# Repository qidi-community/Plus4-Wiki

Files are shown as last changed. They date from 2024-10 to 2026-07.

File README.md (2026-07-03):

# Qidi Community Plus4 Wiki

This is a summary collection of various config tweaks, print profiles, the discussion of, and
links to various printable models that have been developed for improving the user experience
of the Qidi Plus4 3D printer.

## Official Qidi Wiki

### [Qidi Plus 4 Wiki/Support Page](https://wiki.qidi3d.com/en/X-Plus4)

---

## Issues and Possible Fixes

### [Plus4 System Performance Tuning](./content/system-tuning/README.md) or [Alternative version](./content/system-tuning-alt/README.md)

### [Adaptive Main Board Cooling configuration](./content/adaptive-main-board-cooling)

### [SSH Security](./content/ssh-security/README.md)

### [Adding Beacon3D](./content/bed-scanning-probes/Beacon3D/RevH-Normal)

> [!TIP]
> Qidi's 1.7.0 and later updates introduced breaking changes that crash klipper if you have cartographer probe installed. Read the updated cartographer guide below to learn more.
### [Adding Cartographer](./content/bed-scanning-probes/cartographer3d)

### [Modular Tool-Head Mod](./content/modular-toolhead/README.md)

### [Making Z-Offset Permanent](./content/making-z-offset-permanent)

### [Conditional purging and pei wiping to address the cracking of nozzles with ceramic heat-breaks](./content/conditional_purging_and_wiping/README.md)

### [Warming the Chamber Faster!](./content/tuning-for-40-percent-heater-power/README.md)

### [More Accurate Chamber Temperature Measurements](./content/chamber-heater-investigation/README.md)

### [Broken touchscreen firmware](./content/display-firmware-repair/README.md)

---

## (Mostly) Defunct fixes that have been fixed with newer shipping Plus4 models

### [PLA/PETG Heat-creep clogging](./content/nozzle-clogging-tips/README.md) - Fixed by using nozzles with ceramic heatbreaks

### [Chamber Heater Issue](./content/chamber-heater-issue/README.md) - Largely addressed by the v1.6.0 and later firmware

### [SSR Upgrade Mod](./content/heater-ssr-upgrade/README.md) - All Plus4's manufactured after Dec 2024 should already have the fixed SSR's

---

## Printer Configuration Tweaks

### [SSH Access](./content/ssh-access/README.md)

### [Adaptive Chamber Heater Fan](./content/adaptive-chamber-heater-fan/README.md)

### [Dynamic Chamber Temperature Manager](./content/chamber-temperature-manager/README.md)

### [Enhanced Stepper Motor Configuration](./content/stepper-motor-tweaks/README.md)

### [Tweak to Square Corner Velocity](./content/square-corner-velocity/README.md)

### [Enabling KAMP Purge Line](./content/kamp-purging)

### [Enabling SCREWS_TILT_CALCULATE](./content/Screws-Tilt-Adjust/)

### [Better Bed Meshing](./content/more-accurate-bed-meshing/README.md)

### [Disable Wifi Adapter](./content/8188gu-blacklist/README.md)

### [Temperature Change Chimes](./content/temp-chime/README.md)

### [Secure Remote Access](./content/secure-remote-access/README.md)

### [Notes on Heat Soak](./content/Auto Heat Soak for Stock Sensors/README.md)

### [Warp free ASA / ABS prints](./content/warp-free-asa-abs-prints/README.md)

## Orca Slicer Configuration

### [Orca Slicer Settings](./content/orca-slicer-settings)

## Qidi Box

### [Bunny Box - open source Qidi Box using Happy Hare](https://github.com/Wazzup77/Bunny-Box)

---

## Printable Models

### [Ejecta Chute and Catch Bucket](https://www.thingiverse.com/thing:6789666)

### [Ejecta Chute and Catch Bucket - No heatset inserts remix](https://www.thingiverse.com/thing:6794632)

### [Fan duct for the hotend heatsink](https://www.thingiverse.com/thing:6782612)

### [Mainboard cooling](./content/mainboard-cooling/README.md)

### [Mainboard Rear cover that allows use of an 80mm fan](https://www.thingiverse.com/thing:6787302)

### [Lid Hangers](https://www.printables.com/model/1025183-qidi-plus-4-lid-hanger)

### [Filter Exhaust Blocker](https://www.printables.com/model/1037302-qidi-plus-4-filter-exhaust-blocker)

### [Rear Chamber Seal](https://www.printables.com/model/1040774-qidi-plus-4-rear-chamber-cover)

### [HEPA/Activated Carbon filtration system](https://www.printables.com/model/1022271-qidi-plus-4-filtration-system)

### [Exhaust adapter attachment (with CAD)](https://www.printables.com/model/1040218-qidi-plus-4-exhaust-adapter)

### [Lid prop](https://www.printables.com/model/1039528-qidi-plus4-lid-prop)

### [4 inch Duct extraction adapter](https://www.printables.com/model/1036212-qidi-plus-4-4-inch-duct)

### [Hole blocking plate](https://www.printables.com/model/1039152-qidi-4-plus-ports-cover)

### [Push In Place Door Sealing Strip](https://www.thingiverse.com/thing:6801577)

### [Belt Tensioners](https://www.printables.com/model/1044712-qidi-plus4-belt-tensioners/files)

### [WIP - A better chamber thermal sensor mounting position](https://www.thingiverse.com/thing:6802256)

### [Articulating No Hands Door Seal (paid)](https://cults3d.com/en/3d-model/tool/plus4-articulating-no-hands-door-hinge-seal)

### [Articulating No Hands Door Seal (free)](https://www.printables.com/model/1271100)

### [Filament Tangle Sensor Disabler Clip](https://www.printables.com/model/1767439-qidi-plus-4-filament-tangle-blocker-clip)

---

## Additional Software

### [Klippain Shake & Tune v5.1.1 - Qidi Plus 4 Compatible Version](https://github.com/qidi-community/klippain_v511_for_qidi_plus4)

### [(Retired) Klippain Shake & Tune v4.1.0 - Qidi Plus 4 Compatible Version](https://github.com/qidi-community/ShakeTune-For-Plus4)

---

## Aftermarket Parts

### [Replacement hotend heatsink fan - GDSTime GDA30105F (US Store)](https://west3d.com/products/gdstime-dc-24v-30x30x10-axial-fan-24v-gda30105f-dual-ball-bearing-1200rpm-1w-06a-xh2-54)

### [Replacement hotend heatsink fan - GDSTime GDA30105F (EU Store)](https://www.hotend.eu/p/gdstime-axial-fan-sleeve-3010-24v)

### [Replacement hotend heatsink fan - GDSTime GDA30105F (CN Store)](https://www.aliexpress.com/item/1005002857100082.html)

### [Replacement 80 mm mainboard fan - ANVISION (Amazon US)](https://www.amazon.com/ANVISION-2-Pack-Brushless-Cooling-Bearing/dp/B0C18G953Z)

---

## Maintenance Tips

### [Adjusting Belt Tension](./content/adjusting-belt-tension)

### [Lubing Idler Bearings](https://drive.google.com/file/d/1_KHpMQJNxle0u21L5dIt-LYLbkvVnGiD/view)

### [Lubing Rods and Screws](./content/lube-rods-screws)

---

## Hardware Fixes

Some of the first release batches of the Plus 4 have had the occasional hardware issue.
Qidi assures that all customers who contact Qidi support will be looked after.
In the meantime, here are a number of known fixes for the issues that some early adopters are experiencing.

### [Official Qidi Toolhead Bearing Fix](https://drive.google.com/drive/folders/1O0PR0vbxy0Tv7vgcNma1JERQyz9Ir3xW)

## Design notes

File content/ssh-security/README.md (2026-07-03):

# Securing SSH Access

> [!CAUTION]
> FOLLOWING THESE INSTRUCTIONS HAVE THE POTENTIAL TO PERMANENTLY LOCK YOU OUT OF `ssh` ACCESS. PLEASE FOLLOW ALL INSTRUCTIONS CAREFULLY, NOTE DOWN ALL PASSWORDS, AND BACKUP ANY PRIVATE/PUBLIC KEYS AS APPLICABLE.
>
> If you become locked out due to losing access to your password or public/private key-pairs, the only way to restore access would be to perform a factory result with fresh firmware from QIDI and there is no known way to regain access. Only proceed if you can understand and can bear or mitigate the potential risks involved.

By default, the QIDI Plus4 ships with an insecure SSH configuration, allowing simple password access to both the `root` and `mks` accounts. More details on gaining SSH access can be found [here](../ssh-access/README.md).

As such, any bad actor on your local network or with access to the printer's SSH port is able to gain trivial access with full control, allowing for remote code execution, installation of malware, modifying Klipper configs, etc. As such, it's important to secure SSH access to the printer through:

- Changing default passwords [High Importance]
- Disabling root login [High Importance]
- Setting up public/private key authentication [Moderate Importance]
- Disabling password-based SSH login [Moderate Importance]
- Ensuring local-only SSH access through router/network/firewall configuration [Low Importance - Out of Scope]

It is recommended to perform the first four steps in conjunction, as they involve minimal edits to a single file and vastly improve security of your machine.

## Change Default Passwords

The default password for both `root` and `mks` accounts on the Plus4 is `makerbase`. This should be changed for the `mks` password as soon as practicable if the printer is on the network. 

### Prerequisites
- The IP Address of the printer (obtained through the Printer network screen or your router)
- Ability to SSH (WSL on Windows, Terminal on MacOS / Linux)

### Process

SSH into your printer's `mks` account:

```
ssh mks@<ip-address>
```

Type `passwd` to change the password of the `mks` account. It's recommended to use a complex password here, as the `mks` account can gain privileged access through this password.

If you want to keep `root` login, then it is recommended to change the `root` account password too. You can gain `root` account access from the `mks` account with the below command:

```
sudo -i
```

You will be prompted to type the new password that you just set. Then, run `passwd` as the `root` user to change the `root` password. Ideally, it should be different from the `mks` password to prevent simultaneous compromise, though such risks are low. 

## Disabling Root Login

It is recommended to disable the ability to log into the printer as the `root` user, which has superuser privileges. Instead, all SSH logins should be done through a normal user account, and then escalated to `root` with `sudo` as needed. This helps to reduce one potential vector of compromise. 

### Prerequisites
- The IP Address of the printer (obtained through the Printer network screen or your router)
- Ability to SSH (WSL on Windows, Terminal on MacOS / Linux)
- Use of `nano`, `vim,` or `vi` text editor in the command line

### Process

SSH into your printer's `mks` account.

Edit the file found at `/etc/ssh/sshd_config` with `sudo` privileges:

```
sudo nano /etc/ssh/sshd_config
```

Find the line beginning with `PermitRootLogin` and change "yes" to "no". Your end result should look like the below. Mine was found on line 32.

```
PermitRootLogin no
```

Save and exit. Restart the `ssh` daemon with:

```
sudo systemctl restart ssh
```

## Set up Private / Public Key Authentication

Traditionally, SSH authentication is handled with user account passwords. However, passwords can be easily stolen, guessed, or phished and are therefore a less secure means of authentication. Instead, SSH has support for public/private key authentication, whereby a machine generates a key-pair, and the public key of such keypair is shared with the server, and the private key is kept hidden locally. Since these public/private keys are kept cryptographically secure and the private key does not leave your machine in any situation, this is a more resilient form of authentication.

Further details on public/private key authentication is out of scope and can be found [here](https://en.wikipedia.org/wiki/Public-key_cryptography)

As such, it's recommended to enable public/private key authentication to SSH into the printer as opposed to the password-based authentication. You also no longer need to type in your password when SSHing in.

### Prerequisites
- An SSH key-pair has been generated on your computer
  - The exact process varies between OS. Some basic guides are linked below.
    - [WSL/Windows](https://www.howtogeek.com/762863/how-to-generate-ssh-keys-in-windows-10-and-windows-11/)
    - [MacOS/Linux](https://devopscube.com/generate-ssh-key-pair/)
- The IP Address of the printer (obtained through the Printer network screen or your router)
- Ability to SSH (WSL on Windows, Terminal on MacOS / Linux)
- (Optional) The `ssh-copy-id` command **or** a command line text editor (nano / vi / vim)

### Process

There are two options to install the SSH key: (i) automatically with the `ssh-copy-id` command or (ii) manually. If you have the `ssh-copy-id` command in your local computer's command line, it is recommended to use that as it greatly simplifies the process. You can also copy the key manually if preferred, but offers no functional benefits. Most machines will have the `ssh-copy-id` command.

#### Automatic Installation

Once you have generated your SSH key-pair or if you are using an existing SSH key-pair, you will need to copy the ***public*** key of the key-pair onto your printer. ***DO NOT*** under any circumstance, allow your ***private*** key to leave your machine. That is equivalent of a password and should be treated as such. 

Copy the public key to the printer with the following command:

```
ssh-copy-id mks@<ip-address>
```

You will be prompted from the password for the `mks` account. This will install the public key automatically into the `mks` account. You should now be able to `ssh` into the `mks` account without needing to input a password.

#### Manual Installation

If your machine does not have the `ssh-copy-id` command, you will need to copy the key manually. First of all, find the ***public*** key that you generated. Copy the entirety of the public key file. You will need to paste that in a later step.

SSH into your printer:

```
ssh mks@<ip-address>
```

Edit the file found at `~/.ssh/authorized_keys`. This is the listing of all SSH public keys which are allowed to access the printer. You do not need superuser privilege to edit this file.

```
nano ~/.ssh/authorized_keys
```

Paste in the ***public*** key that you copied earlier. You have now installed the SSH public key and you should be able to `ssh` into the `mks` account without needing to input a password.

## Disable Password Authentication

If you are using private / public key authentication with your printer and do not need password authentication, it is recommended that you disable the ability to SSH into the printer with a password. This vastly improves security, particularly if your password is less complex, reused, or easy to guess. While a strong password mitigates the risk significantly, it is still recommended to remove SSH password access to reduce the attack surface. 

### Prerequisites
- The IP Address of the printer (obtained through the Printer network screen or your router)
- Ability to SSH (WSL on Windows, Terminal on MacOS / Linux)
- SSH private / public key authentication set up and working
- Use of `nano`, `vim,` or `vi` text editor in the command line

#### Warning!!!

If you disable password authentication, you will not be able to SSH into your printer except with the private / public key(s) you have set up. Please be mindful that if you lose your private / public key access, you will not be able to SSH into the printer at all, and will need to undergo a complete factory reset. QIDI will not be able to recover access for you, and there is no (known) way to bypass this. Before doing this, it is recommended you have at least two devices with different SSH key-pairs set up for access, in case you lose your primary device.

### Process

SSH into your printer:

```
ssh mks@<ip-address>
```

Edit the file found at `/etc/ssh/sshd_config` with `sudo` privileges:

```
sudo nano /etc/ssh/sshd_config
```

Make the following changes to these SSH parameters within the file:

```
PasswordAuthentication no
ChallengeResponseAuthentication no
UsePAM no
```

`ChallengeResponseAuthentication` may already be set to `no`. If so, no changes to that line are needed.

Save and exit. Restart the `ssh` daemon with:

```
sudo systemctl restart ssh
```

Password login should now be disabled for the printer, and you must login with one of the existing private / public key pairs.

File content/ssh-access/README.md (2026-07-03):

# How to access your Plus 4 through SSH

SSH access is needed to interact with the Klipper configuration system. You will specifically need to SSH into your printer to add Klipper extensions.

To log into your printer, first detrmine it's IP address from the front panel's network tab.

Then open a shell (or Terminal on Windows) and type:

```ssh mks@x.x.x.x``` 

Where x.x.x.x is the IP address.

The password is **makerbase**

Common config files are in /home/mks/printer_data/config

You can also use popular FTP client filezilla, with Host sftp://IP_ADDRESS (user and pass as above) , then right click a file, choose View/Edit, when you save, go back to filezilla and it will ask if you want to re-upload changes.

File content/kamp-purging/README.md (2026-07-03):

# Enabling KAMP Purging

KAMP Purging draws a single short ~30mm long, ~2mm wide, and ~0.8mm tall line near the front left of the area that the model will occupy.

This serves a similar purpose to the stock Qidi purge patterns by clearing the nozzle of any oozing material just before starting the first print object.

The KAMP Purge line uses about the same amount of filament as the stock Qidi purge pattern.

The main complaint about the stock Qidi purge pattern is that it can be difficult to remove cleanly. This can result in touching the build surface area excessinvely, possibly leaving oily residue from fingers. In turn, _this_ can then affect surface adhesion quality for future prints until the plate is cleaned/washed again.

The KAMP purge line, being thicker and shorter, makes it easy to flick off the build surface with a fingernail, resulting in less contact with the build plate.

** While these are valid advantages, you can also try using a 5-10 loop skirt, as this lets you check/test your 1st layer z-height across the whole build area perimeter and is easier to remove than the default single line. - hayden.

## How to Enable

TL;DR Doing the following will enable the `LINE_PURGE` macro in Klipper, which we will use later.

First we must edit the `KAMP_Setting.cfg` file, which lives in the same directory as `printer.cfg`

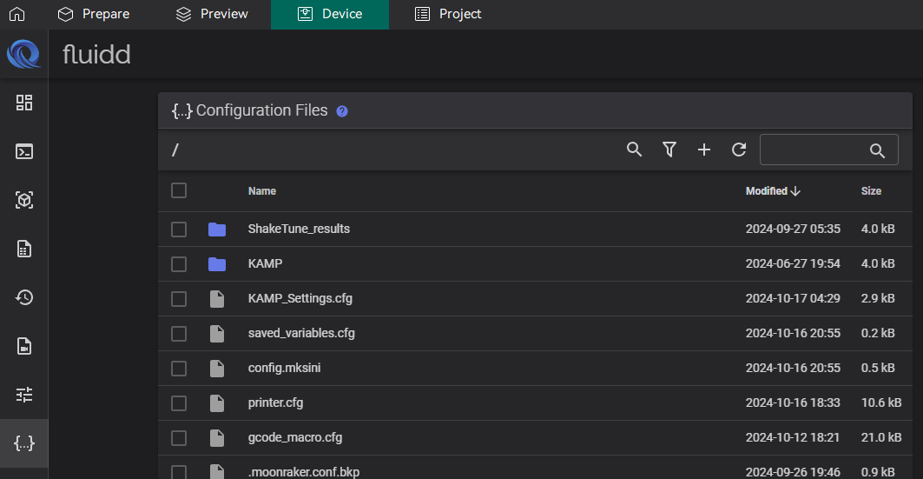
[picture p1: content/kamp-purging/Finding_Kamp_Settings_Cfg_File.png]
Where to find KAMP_Settings file


or go to directory `/home/mks/printer_data/config` if you're using [SSH](https://github.com/qidi-community/Plus4-Wiki/tree/main/content/ssh-access).

Uncomment the line `[include ./KAMP/Line_Purge.cfg]`.

> [!TIP]
> If you plan on printing with TPU, I also recommend changing the `variable_flow_rate` setting to a value of `4`.
The default of `12` here is way too high for TPU, and possibly some other filament types, and can cause oozing and extruder issues.

### Restart the Printer

If you've edited the files through Fluidd, Use the orange "Save & Restart" button up top

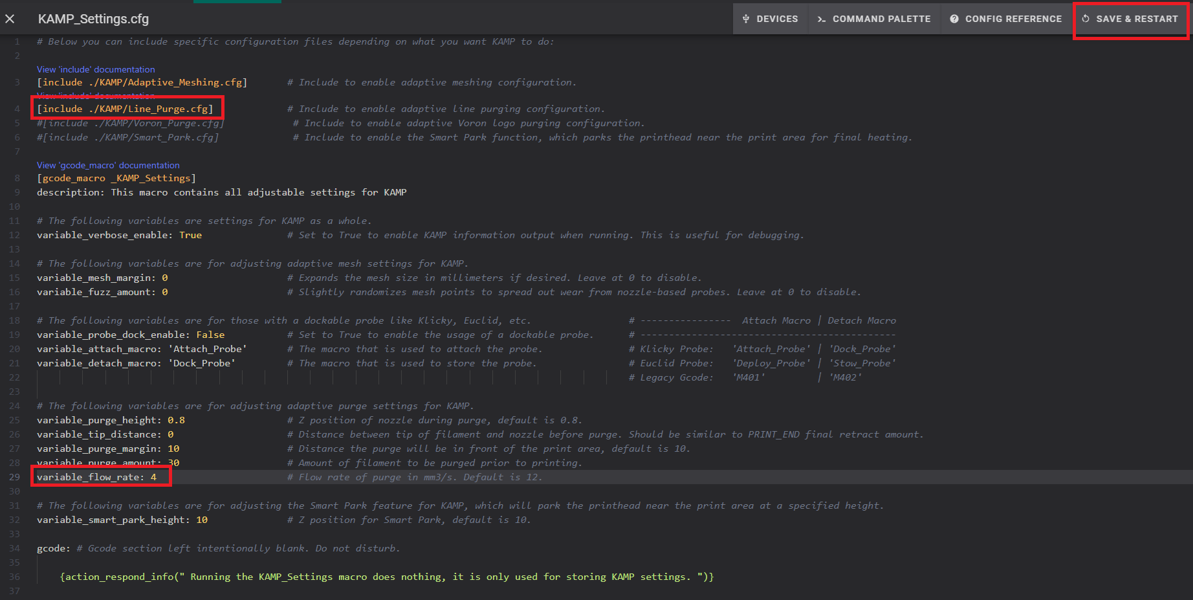
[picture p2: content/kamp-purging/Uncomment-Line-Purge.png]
Uncommenting KAMP's Line Purge Config


If you used SSH, please note that the files you've just edited are not necessarily written to disk yet. 
To force this to happen, run the command `sync`. If that comes back with no further remarks and has an exitcode of `0`, you can powercycle the printer.

SSH check exitcode sync

## Editing the Printer's Start G-Code in the slicer

The stock Qidi purge pattern is created by a set of lines in the Printer's Start G-Code definition in the slicer.

The Qidi Purge Pattern G-Code will look like this:

```
G0 Z[initial_layer_print_height] F600
G1 E3 F1800
G1 X{(min(print_bed_max[0] - 12, first_layer_print_min[0] + 80))} E{85 * 0.5 * initial_layer_print_height * nozzle_diameter[0]} F3000
G1 Y{max((min(print_bed_max[1] - 3, first_layer_print_min[1] + 80) - 85), 0) + 2} E{2 * 0.5 * initial_layer_print_height * nozzle_diameter[0]} F3000
G1 X{max((min(print_bed_max[0] - 12, first_layer_print_min[0] + 80) - 85), 0)} E{85 * 0.5 * initial_layer_print_height * nozzle_diameter[0]} F3000
G1 Y{max((min(print_bed_max[1] - 3, first_layer_print_min[1] + 80) - 85), 0) + 85} E{83 * 0.5 * initial_layer_print_height * nozzle_diameter[0]} F3000
G1 X{max((min(print_bed_max[0] - 12, first_layer_print_min[0] + 80) - 85), 0) + 2} E{2 * 0.5 * initial_layer_print_height * nozzle_diameter[0]} F3000
G1 Y{max((min(print_bed_max[1] - 3, first_layer_print_min[1] + 80) - 85), 0) + 3} E{82 * 0.5 * initial_layer_print_height * nozzle_diameter[0]} F3000
G1 X{max((min(print_bed_max[0] - 12, first_layer_print_min[0] + 80) - 85), 0) + 3} Z0
G1 X{max((min(print_bed_max[0] - 12, first_layer_print_min[0] + 80) - 85), 0) + 6}
```

> [!TIP]
> If you don't feel comfortable at first to delete the lines, you can "comment them out" by adding a `;` at the start of the line. You can always return to delete them later.
> Comment instead of delete

We want to remove those lines and put `LINE_PURGE` in their place, like so.

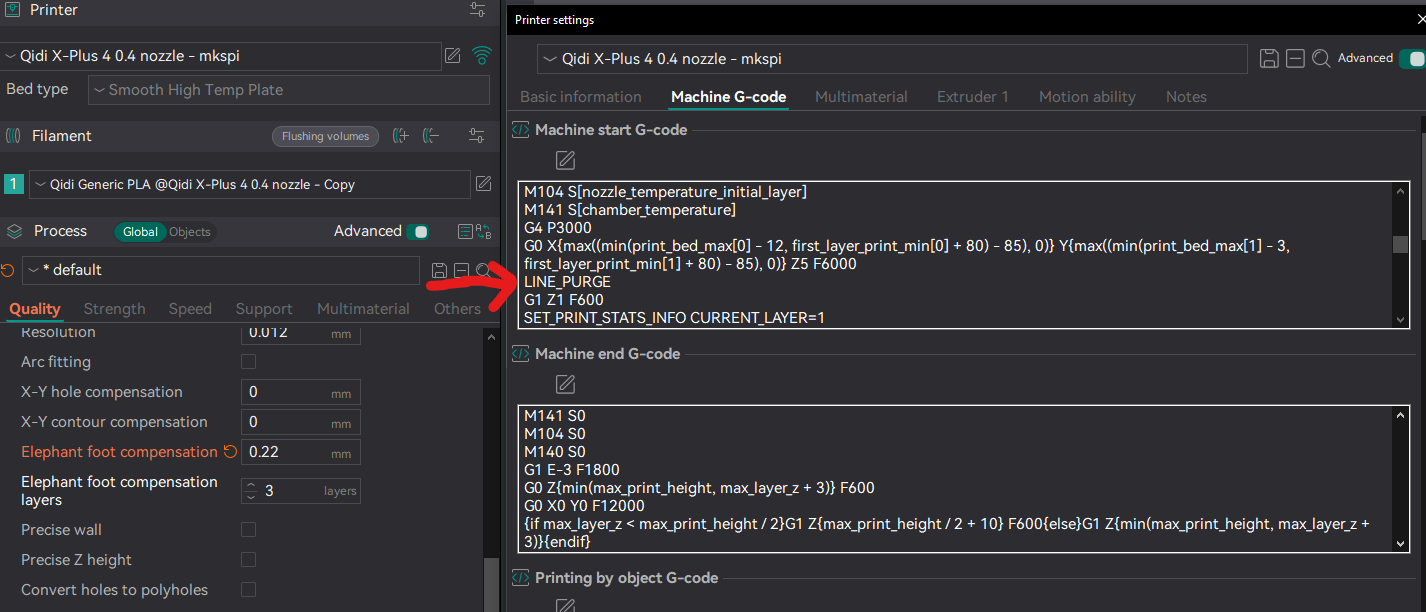
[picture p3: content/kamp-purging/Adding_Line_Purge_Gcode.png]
Modifying Slicer Printer Start G-Code


Restart klipper.
Now you have an easy to remove purge line that takes up less of the build area.

> [!NOTE]
> At the start of a print during KAMP purging you might notice a comment in the console about turning on firmware retraction. Ignore this. It is not necessary and slicer based retraction is superior.

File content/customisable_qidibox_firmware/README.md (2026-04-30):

# A modified replacement set of firmware files and customisable QidiBox macros for the Qidi Plus 4

## Disclaimer

All of the work here is very strongly a Work In Progress.  If you wish to use it, please accept that this is provided with no guarantees.

#  What is this?

The following moves a significant portion of the QidiBox filament changing, purging, and cleaning out of the obfuscated `*.so` files that the QidiBox firmware ships with, and into a single gcode macro config file that can be easily edited to modify the behaviour of the g-code macros.  Additionally more generic filament change macros are added that allows for the QidiBox to be used with OrcaSlicer (tested), QidiStudio (tested), BambuStido (untested) and PrusaSlicer (maybe?)

## Patching Qidi Plus 4 firmware

Using an SSH shell to the printer, perform the following changes:

The following files may be used to replace their `*.so` equivalents in the `/home/mks/klipper/klippy/extras/` directory

- [/home/mks/klipper/klippy/extras/aht20_f.py](./aht20_f.py)
- [/home/mks/klipper/klippy/extras/box_detect.py](./box_detect.py)
- [/home/mks/klipper/klippy/extras/box_extras.py](./box_extras.py)
- [/home/mks/klipper/klippy/extras/box_rfid.py](./box_rfid.py)
- [/home/mks/klipper/klippy/extras/box_stepper.py](./box_stepper.py)
- [/home/mks/klipper/klippy/extras/buttons_irq.py](./buttons_irq.py)

Now move/backup the corresponding `*.so` files out of the same directory to somewhere safe where they won't be picked up by the Klipper firmware. After this, you can use the following commands to overwrite them:

```
cd ~/klipper/klippy/extras/

sudo rm -f aht20_f.so box_detect.so box_extras.so box_rfid.so box_stepper.so buttons_irq.so

wget https://raw.githubusercontent.com/qidi-community/Plus4-Wiki/refs/heads/main/content/customisable_qidibox_firmware/aht20_f.py

wget https://raw.githubusercontent.com/qidi-community/Plus4-Wiki/refs/heads/main/content/customisable_qidibox_firmware/box_detect.py

wget https://raw.githubusercontent.com/qidi-community/Plus4-Wiki/refs/heads/main/content/customisable_qidibox_firmware/box_extras.py

wget https://raw.githubusercontent.com/qidi-community/Plus4-Wiki/refs/heads/main/content/customisable_qidibox_firmware/box_rfid.py

wget https://raw.githubusercontent.com/qidi-community/Plus4-Wiki/refs/heads/main/content/customisable_qidibox_firmware/box_stepper.py

wget https://raw.githubusercontent.com/qidi-community/Plus4-Wiki/refs/heads/main/content/customisable_qidibox_firmware/buttons_irq.py

```

## Adding the new customisable macros 

Using the FLUIDD Web UI, add in the following [box_macros.cfg](./box_macros.cfg) file into the same directory as your `printer.cfg` file

Then edit your printer.cfg and add in the following line below the existing `[include box.cfg]` line:

```
[include box_macros.cfg]
```

Now click `SAVE & RESTART`

> [!WARNING]
>  It is possible that some macros (for example, `EXTRUSION_AND_FLUSH`) are already defined in your `gcode_macro.cfg` file. Double check that you aren't creating duplicate gcode_macro definitions!

After the printer has restarted (hopefully no errors show up - if they do, address them), then you will need to power-cycle the printer to activate the new firmware changes.

## Update your slicer's Plus 4 macros

Within the `Machine start G-code` section ensure that the `PRINT_START` line has `EXTRUDER=[initial_no_support_extruder]` appended to it, such that it appears like so:

```
PRINT_START BED=[bed_temperature_initial_layer_single] HOTEND=[nozzle_temperature_initial_layer] CHAMBER=[chamber_temperature] EXTRUDER=[initial_no_support_extruder]
```

Within the `Change filament G-code` section, replace its entire contents with the following:

```
{ if current_extruder != next_extruder }
SET_GCODE_VARIABLE MACRO=BOX_CHANGE_FILAMENT VARIABLE=max_layer_z VALUE={max_layer_z}
SET_GCODE_VARIABLE MACRO=BOX_CHANGE_FILAMENT VARIABLE=flush_length_1 VALUE={flush_length_1}
SET_GCODE_VARIABLE MACRO=BOX_CHANGE_FILAMENT VARIABLE=flush_length_2 VALUE={flush_length_2}
SET_GCODE_VARIABLE MACRO=BOX_CHANGE_FILAMENT VARIABLE=flush_length_3 VALUE={flush_length_3}
SET_GCODE_VARIABLE MACRO=BOX_CHANGE_FILAMENT VARIABLE=flush_length_4 VALUE={flush_length_4}
SET_GCODE_VARIABLE MACRO=BOX_CHANGE_FILAMENT VARIABLE=current_extruder VALUE={current_extruder}
SET_GCODE_VARIABLE MACRO=BOX_CHANGE_FILAMENT VARIABLE=current_filament_extrude_rate VALUE={old_filament_e_feedrate}
SET_GCODE_VARIABLE MACRO=BOX_CHANGE_FILAMENT VARIABLE=current_filament_high_temp VALUE={nozzle_temperature_range_high[current_extruder]}
SET_GCODE_VARIABLE MACRO=BOX_CHANGE_FILAMENT VARIABLE=current_filament_retract_length VALUE={old_retract_length_toolchange}
SET_GCODE_VARIABLE MACRO=BOX_CHANGE_FILAMENT VARIABLE=next_extruder VALUE={next_extruder}
SET_GCODE_VARIABLE MACRO=BOX_CHANGE_FILAMENT VARIABLE=next_filament_extrude_rate VALUE={new_filament_e_feedrate}
SET_GCODE_VARIABLE MACRO=BOX_CHANGE_FILAMENT VARIABLE=next_filament_temp VALUE={new_filament_temp}
SET_GCODE_VARIABLE MACRO=BOX_CHANGE_FILAMENT VARIABLE=next_filament_high_temp VALUE={nozzle_temperature_range_high[next_extruder]}
SET_GCODE_VARIABLE MACRO=BOX_CHANGE_FILAMENT VARIABLE=next_filament_retract_length VALUE={new_retract_length_toolchange}
SET_GCODE_VARIABLE MACRO=BOX_CHANGE_FILAMENT VARIABLE=retraction_distance_when_cut VALUE=0
BOX_CHANGE_FILAMENT C_FILA_TYPE='{filament_type[current_extruder]}' N_FILA_TYPE='{filament_type[next_extruder]}'
{endif}
```

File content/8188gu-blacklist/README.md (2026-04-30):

# Disabling Wifi 8188gu module
As of QIDI's latest Plus4 firmware release, 1.6, the USB wireless module included 
in current machines is using an rtlink dongle that is creating a kernel thread that
is consuming considerably more CPU cycles than is expected. Due to the finite 
compute available on the SOC, it's best to preserve it for klipper. 

This can be achieved in by simply removing the dongle from the Plus4 system board or
more dramatically disabling the driver module from loading when the printer is
booting up. 

## Confirm The Issue
The easiest way to observe impact is running the `top` or `htop` commands from
the command line. If you see `RTW_CMD_THREAD` and CPU is high, you are impacted. In this screenshot, the user's printer is consuming a considerable amount of CPU at 24.3%

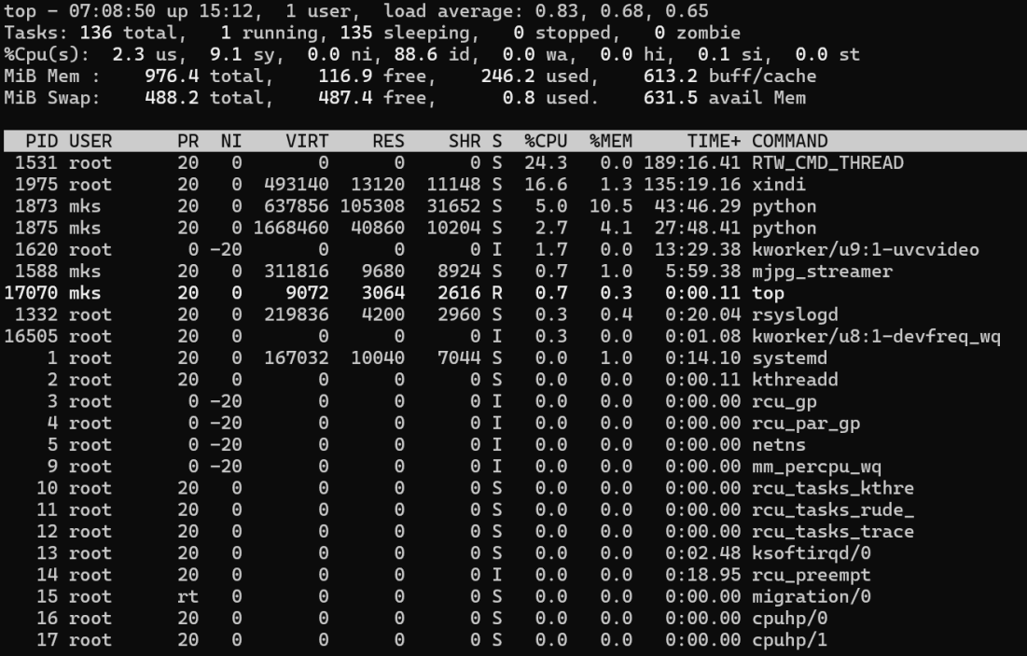
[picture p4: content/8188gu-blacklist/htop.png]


## Option 1: Unplug the module from the board
Remove the system fan board cover and examine the USB ports on the side right side of
the board. The USB dongle looks like this, but could vary:

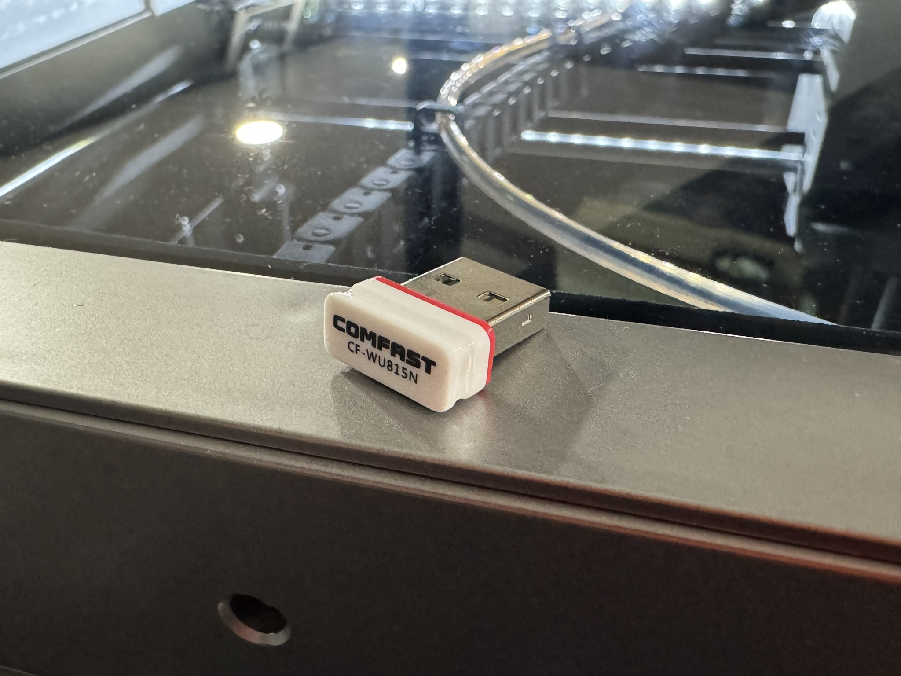
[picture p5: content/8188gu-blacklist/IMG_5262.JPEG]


Once removed, you need to restart your printer so the module isn't loaded. Until the
machine is restarted, the module will remain loaded and continue to needlessly consume
CPU cycles.

## Option 2: Blacklist the Driver Module
If you'd rather NOT remove the dongle, you can simply blacklist the module from loading
in the first place. To do so, run the following commands:

ssh into your 3D Printer's Linux command shell (see [ssh-access](https://github.com/qidi-community/Plus4-Wiki/tree/main/content/ssh-access) for details)

```
sudo -i
cd /etc/modprobe.d
ls -l
echo "blacklist 8188gu" > blacklist-8188gu.conf
echo "blacklist cfg80211" > blacklist-cfg80211.conf
echo "blacklist rfkill" > blacklist-rfkill.conf
ls -l
```
Verify that 3 new blacklist-*.conf files exist. If that's that case execute this command:
```
update-initramfs -u
```

## Restart the Printer

> [!NOTE]
> If you've edited the files through Fluidd, Use the orange "Save & Restart" button up top

The files we've just edited are not necessarily written to disk yet. 
To force this to happen, run the command `sync`. If that comes back with no further remarks and an exitcode of `0`, you can powercycle the printer.



## Validate The Fix
Once you have restarted your Plus4, connect via `ssh` to your printer again and run the following command:

```
for MODULE in 8188gu cfg80211 rfkill ; do lsmod | grep -qw "${MODULE}" && echo "Module '${MODULE}' is loaded." || echo "Module '${MODULE}' is NOT loaded." ; done
```

## Uninstall 

Remove the 3 files 

```
sudo -i
cd /etc/modprobe.d
rm -f blacklist*.conf
```
update the bootloader
```
update-initramfs -u
```
and `sync` and power cycle.

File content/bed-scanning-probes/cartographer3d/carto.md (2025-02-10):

The Carto install guide for the Plus4 has been relocated to [here](https://github.com/qidi-community/Plus4-Wiki/blob/main/content/bed-scanning-probes/cartographer3d/README.md)

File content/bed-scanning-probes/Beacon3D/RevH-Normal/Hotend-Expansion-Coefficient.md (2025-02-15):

# Hotend Expansion Co-efficient Calibration

Calibrating the thermal expansion of the hotend is frustratingly difficult.  If you've decided that you don't have enough drama in your life already, or simply hate yourself, then proceed.

## Goals & Requirements

- Measure as wide of a range as possible across multiple reference points.
- Clear any bed mesh and all Z offset adjustments
- Use lots of heat soaking for the hotend at 50C, and then at 250C.  Basically 2 minutes worth.
- Probe the same reference point multiple times.  

## Preparation

Preparation of the hotend and nozzle are absolutely critical for reliable results.

Important factors:

- Do NOT use PLA to start with.
  * It will crystallise and ooze and generally be the enemy of all repeatability.
  * Instead flush it out with some higher temperature filament like PET or PA, and then proceed to cold pull
- Cool-pull any filament from hotend.
  * Start with the hotend being cold.
  * Press the motors off button on the UI so the extruder stepper motor is disengaged.
  * Then turn on the hotend and keep pulling up on the filament until it yanks out at the earliest opportunity.
  * This minimises any stringing and it'll just come out pretty much with the shape of the internal nozzle cavity intact
- Make sure nozzle has been tightened at 300C to minimise the impact joint expansion around the threads
- Poke the nozzle orifice with a fine needle dislodge any filament.  We want absolutely NO oozing at all
- Thoroughly clean the nozzle with a wire brush at 300C to remove any debris.  We want that nozzle tip to be as clean as possible.
- Heat bed to 50C and heat-soak for uniformity

## Helper Macro

I have created a calibration macro that automates the calibration process.  You may [find it here](./beacon_calibrate.cfg)

Copy that macro file to its own file in your printer configuration directory, and include it from your `printer.cfg` file.  Save and restart

The macro may be run with the following console command: `BEACON_CALIBRATE_THERMAL_EXPANSION`

I will stress once again that the nozzle and hotend MUST be cleaned and prepared properly before using this macro,
otherwise it will almost assuredly yield junk results, with the most common outcome being a gross under-representation of the true thermal expansion co-efficient by 50% or possibly worse.
I simply cannot stress this enough how critical having a thoroughly clean hotend without any filament in, or attached, to it is of the greatest importance.

## My Personal Run results

Each run takes about 30 minutes on the Plus 4, with a 20 minute cool-down between runs:

- Nozzle thermal expansion over 200C is 0.0872143mm  =>  0.0004361 mm/°C
- Nozzle thermal expansion over 200C is 0.0910357mm  =>  0.0004552 mm/°C
- Nozzle thermal expansion over 200C is 0.0891429mm  =>  0.0004457 mm/°C

_**Average of those 3 is 0.0004457 mm/°C ± 2.1%**_

From this, and due to the variability, I chose to adopt an expansion co-efficient of 0.00045 mm/°C in practical use.

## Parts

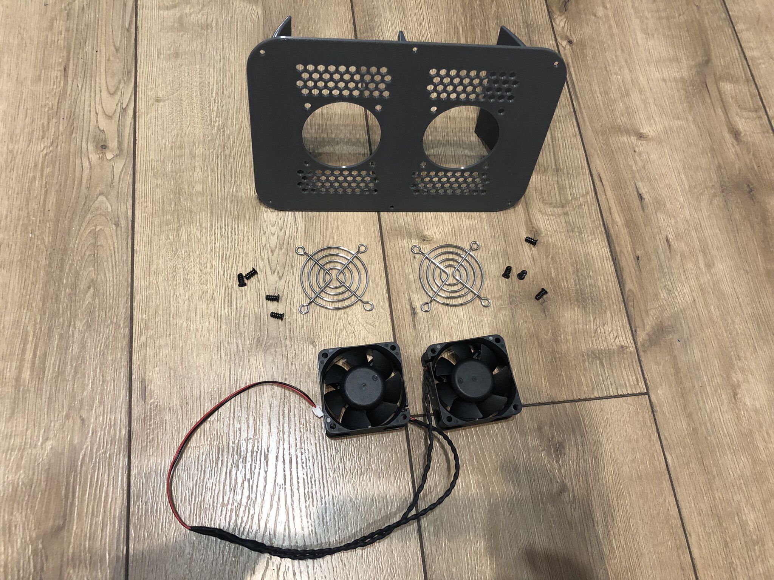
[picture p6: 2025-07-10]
content/mainboard-cooling/img/parts.JPEG

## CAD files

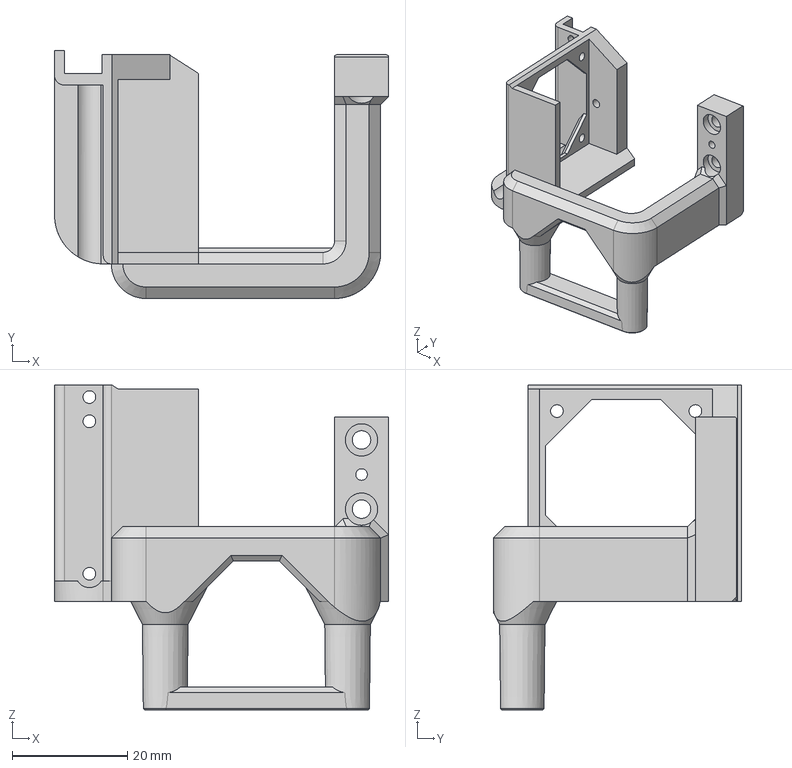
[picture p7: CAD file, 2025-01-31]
content/bed-scanning-probes/Beacon3D/RevH-Normal/Combo-Mount.step
57.9 x 43.0 x 56.3 mm

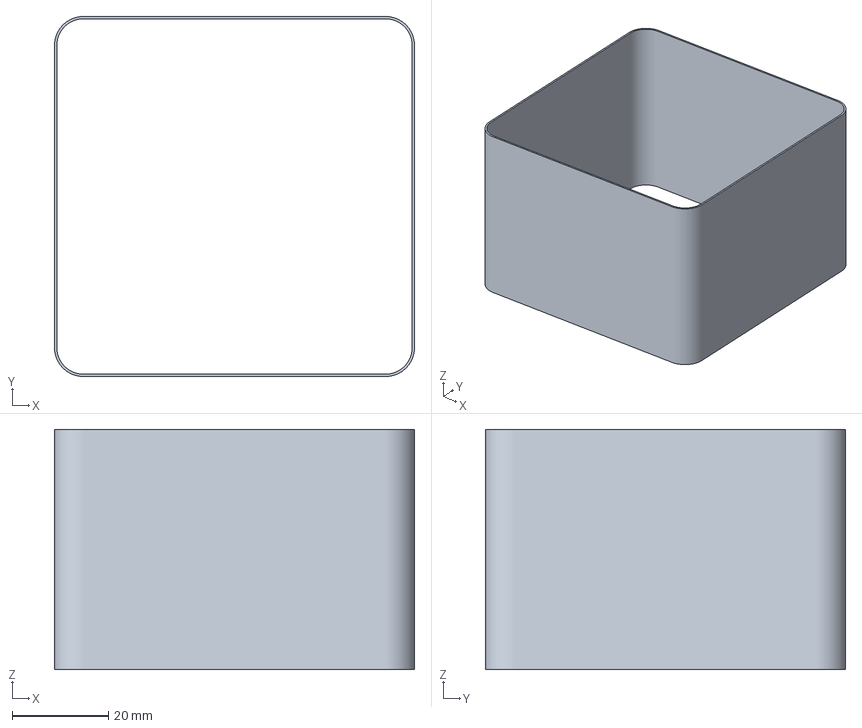
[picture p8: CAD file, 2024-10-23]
content/troubleshooting-vfa/VFA_TEST.3mf
75.0 x 75.0 x 50.0 mm

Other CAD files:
content/troubleshooting-vfa/VFA_TEST.stl

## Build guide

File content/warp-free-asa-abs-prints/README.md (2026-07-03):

### Warp free ASA / ABS prints

Well that is a big claim, and Im not saying it will fix all problems, as there can be many reasons for this, but I found several related problem with orca slicers default filament settings, that was causing the corners of my prints to warp up.

First I just want to highly recommend "Filaform bed adhesive spray" the stuff works wonders, and is much cleaner, easier to work with, stronger, and last longer than glue stick.

But thats not what this is about, as even with that i was still getting warp...

What it turned out to be were 3 settings in the filament "Cooling" menu:
* "No cooling for the first"
* "Min fan speed threshold"
* "Keep fan always on"

See ASA/ABS is very sensitive to cooling, and generally you dont need any parts cooling, but at high speed and or/and short layer time (small parts) it is still needed.

But having it on always, even at 10% at the start is a killer.

By default it is set with "No cooling for the first" = 3 layers which helps, but its too little, the print is still tee flexible at only 3 layer high, so i recommend 10-15 layers first.

Also I set  "Min fan speed threshold" to 0, (from 10) as you want it to not run at all if its a large enough part that is being printed. I set the layer time to 40s. (I have max set to 50% and 4s. Thes 2 can be tweaked, by looking at the "Fan Seed" display mode in the part preview once sliced you can see what the speed will be at centain layers and areas.

And finally the other killer is "Keep fan always on", this also is not needed and should be unticked, this allows  0% fan when not needed, creating the strongest warp free prints possible, while it still being able to ramp up for small detail, bridges & overhangs.

Here is an example





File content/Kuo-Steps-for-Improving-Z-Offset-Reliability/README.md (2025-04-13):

# Kuo Steps for Improving Z-Offset Reliability
Qidi Plus 4 printers come equipped with nozzle touch and bed proximity sensors to enable automatic z-offset, bed leveling, and per-print meshbed functionality. User expectation is that the printer will automatically level the bed and repeatably set nozzle distance accurately for printing. Unfortunately, stock Plus4 implementaiton is not entirely reliable. Multiple owners have reported unreliable first layers, or even gouged print plates despite ABL sensors. 

I use multiple strategies from the community wiki to improve odds of accurate and repeatable z-offset and bed mesh. To the wiki recommendations, I have added tweaks based upon days of sensor reliablity testing at various temperatures, speeds, and probing distances. An entire chain of things must happen correctly for first layer accuracy. Break any item in the chain, and the result is flawed first layer bed / nozzle positioning. 

# Terms Used
Reading online advice on z-offset, bed tramming, and bed mesh can be confusing because the same phrase, z-offset, is used for mutiple different things. For the purposes of this discussion I define the some terms to differentiate various z-offset meanings. They may not be exactly how Klipper and Qidi firmware implement or name them, but are needed to convey the concepts.

## z-screw-position-count: 
This is the underlying z-screw position that Klipper tracks. It is kept by the system counting and keeping track of how many steps the motors have been moved.

## z-nozzle-touch: 
This is the z at which the system detects nozzle touching print bed. It is the zero point of the z coordinates for printing. 

## z-offset-internal: 
The printer has a formula determined distance that it considers the correct position for first layer when z-offset-user is zero.

## z-offset-user: 
This is the z-offset that users set. It is in added to the z-offset-base. If you set z-offset-user to place bed 0.1 mm below nozzle, the actual bed to nozzle distance is your z-offset-user combined with z-offset-internal.

## stored-Z-offset: 
Qidi firmware tries to store z-offset-user at the end of each print job. This feature is intended to let users manually tweak z-offset via the printer control panel and have their adjustment stored for later print jobs.

## bed-mesh: 
This is an induction probe mapping of bed shape created by probing the print plate. The zero for these measurements is calibrated by the printer measuring induction probe reading vs z-nozzle-touch. After that calibration, all distances from nozzle to bed are done via induction probe rather than nozzle touch. 

The bed mesh measurements are used to moved the bed up/down to compensate for bed height variation. The printer attempts to keep nozzle distance equal to z-offset-internal + z-offset-user. The percent of bed mesh compensation varies with z-height. Typically, printers fade out bed compensation after several layers height printing.

As a KAMP printer, there are actually two bed meshes potentially in use. The default mesh is that saved after performing a "tune" mesh bed operation. That is the whole print bed mesh and can serve as the bed mesh when a KAMP mesh is not available. Print jobs on the Qidi Plus4 typically include a KAMP mesh measurement step wherein a more specific bed mesh of the actual print area is done. The print job then uses the KAMP mesh to do  bed mesh compensation rather than the default mesh.

Note: Because the vast majority of distance measurements are performed using the induction probe which is re-calibrated with nozzle touch, accuracy of BOTH nozzle touch and induction probe are needed for bed mesh, bed z-tilt, and bed mesh compensation. 

NB: Induction probes (and even Beacon probes) do not measure reliably near the edges of the print plate. Also, probe offset and mechanical limits mean the printer can never actually take measurements of bed mesh all the way out to print bed edges. Therefore, bed mesh may be dramatically wrong when printing is at extreme edge of bed.

# Problems on the Qidi Plus 4:

a: Piezo bed sensors at incorrect pre-tension: Nozzle touch sensing becomes unreliable at low PLA bed temperatures, and increasingly worse at high bed temperatures.

b: Piezo bed sensor mechanically damaged or poorly made: Piezo sensor discs are bonded to their brackets using glue. There are reports of a batch of sensor discs having  glue that deteriorates at high temperatures. Also, hard impacts to print bed can overstress mounting glue for the sensor discs. The majority of piezo sensor are okay, but if they break, z-nozzle-touch may not be detected. As a result, the user sees x-carriage lifted during nozzle touch and subsequently suffer a gouged print plate. Z-nozzle-touch was incorrectly detected too high (too late). Once piezo sensors fail, they need to be replaced or possibly repaired via re-bonding.

c: Bed downward mechanical stop is uneven without leveling blocks due to shape of platform bottom: Letting the printer lower bed to bottom, without leveling blocks, does not repeatably bottom out the z screws in same position. Leveling blocks must be used. These should be exactly the same height and provide a SOLID stop for both left and right z-screws. 

d: Z-stepper motor microstepping and driver interpolation settings in firmware 1.6.0 may cause a Klipper issue with accuratetly counting and tracking z position.

e: Induction probe accuracy and reliability are not fully optimized in firmware 1.6.0. The firmware settings for probing distance and speed fail to work properly with some induction probes. The default 5 mm distance and 5 mm/sec speed works for most induction probes, but for some units, the distance especially, is too short. The bed must move far enough to be reliably out of hysteresis range of the induction probe. My measurements suggest that at least 6.5 mm probing distance is needed to be compatible with probes that trigger at a longer distance.

f: Stored-Z-offset unpredictably changes. Users report stored z-offset can mysteriously become zero or seem to stack up over a series of prints. The exact mechanism or circumstances of this happening are not yet known.

# What I Do (After Removing Packing Materials)

## 1. Download and install firmware 1.6.0. 
Everything I describe here is with firmware 1.6.0

## 2. Set Piezo Sensors to Reasonble Pre-tension
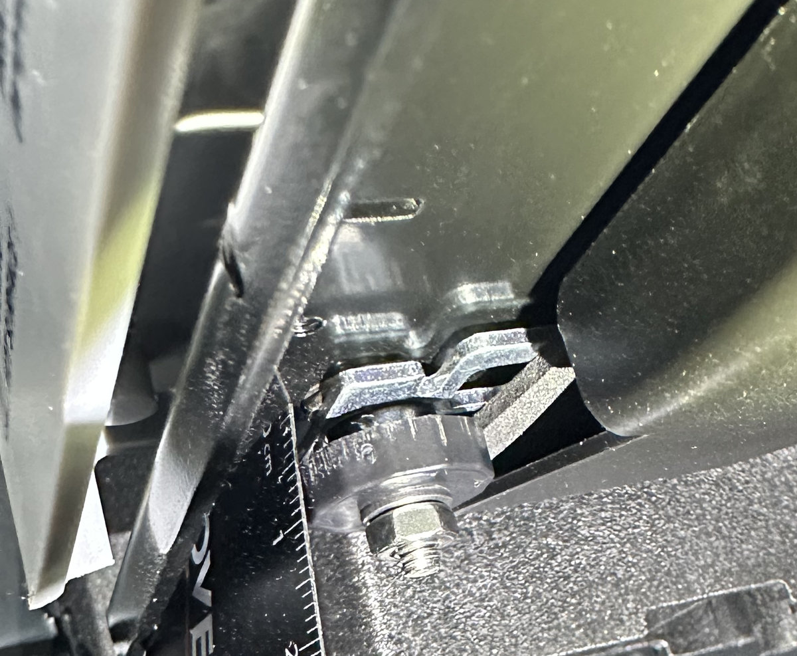
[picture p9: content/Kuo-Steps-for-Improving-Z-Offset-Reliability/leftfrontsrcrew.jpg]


Before doing any bed leveling, set bed screw knobs to position the bottom of the plastic knobs to 9-10 mm away from bottom of metal bed plate above. If your printer has just the locking nut (no lock washer), that leaves about three threads visible below lock nut. Once at this position, lock the front left screw in place. Leave that screw alone. Do bed leveling ONLY with the other three screws. That should keep you in good pre-tension range for all four piezos.

## 3&4 Preamble: 
For background, see Better Bed Meshing, https://github.com/qidi-community/Plus4-Wiki/blob/main/content/more-accurate-bed-meshing/README.md
Do NOT just follow that guide. I do NOT do everything identically to the wiki and I add crucial steps.

# 3. Z /Z1 Stepper and Driver Settings for Better Kiipper Z tracking
Follow the instructions the wiki to set printer.cfg

Microsteps to 16

in stepper sections...

```
[stepper_z]
step_pin:U_1:PB1
dir_pin:U_1:PB6
enable_pin:!U_1:PB0
microsteps: 16 ;<---------
rotation_distance: 4
full_steps_per_rotation: 200
endstop_pin:probe:z_virtual_endstop # U_1:PC3 for Z-max
endstop_pin_reverse:tmc2209_stepper_z:virtual_endstop
position_endstop:1
position_endstop_reverse:285
position_max:285
position_min: -4
homing_speed: 10
homing_speed_reverse: 10
second_homing_speed: 5
homing_retract_dist: 5.0
homing_positive_dir:false
homing_positive_dir_reverse:true
#step_pulse_duration:0.0000001

[stepper_z1]
step_pin:U_1:PC10
dir_pin:U_1:PA15
enable_pin:!U_1:PC11
microsteps: 16 ;<---------
rotation_distance: 4
full_steps_per_rotation: 200
endstop_pin_reverse:tmc2209_stepper_z1:virtual_endstop
#step_pulse_duration:0.0000001
```

Also follow the instructions there to set in sections...

```
[tmc2209 stepper_z]
uart_pin:U_1: PB7
run_current: 1.07
# hold_current: 0.17
interpolate: False ;<-----
stealthchop_threshold: 9999999999
diag_pin:^U_1:PA13
driver_SGTHRS:100

[tmc2209 stepper_z1]
uart_pin:U_1: PC5
run_current: 1.07
# hold_current: 0.17
interpolate: False ;<-----
stealthchop_threshold: 9999999999
diag_pin:^U_1:PC12
driver_SGTHRS:100
```

# 4. Induction Probing Distance and Speed
My testing at multiple bed temperatures, probing speeds, and distances demonstrates that the firmware 1.6.0 speed and distance are not optimal. Probing distances of 6.5 mm or greater yields fewer pre-triggered sensor errors than the stock 5 mm. Probing speed is less critical, and can actually probe faster than the stock 5 mm/sec.

My settings for [smart_effector] and [bed_mesh] are below. Comments are at my changes.
Be mindful of spaces. There must be a space after the number and before ;comment

````
[smart_effector]
pin:U_1:PC1
recovery_time:0
x_offset: 25
y_offset: 1.3
z_offset: 0.000001
speed: 5 ; probing speed
lift_speed:18 ;faster drop away from probe
probe_accel:50
samples: 1 ;leave this at two until you verify probe is reliable
samples_result: submaxmin
sample_retract_dist: 8 ;probing distance
samples_tolerance: 0.025 ;no greater than this for tolerance
samples_tolerance_retries:5

[bed_mesh]
speed: 600 ;faster xy move between sample locations
horizontal_move_z: 5 ;probing speed
mesh_min:25,10
mesh_max:295,295
probe_count:9,9
algorithm:bicubic
bicubic_tension:0.4
mesh_pps: 2,2
````

Before dropping samples down to 1, verify that your speed and distance settings achieve at least four full bed meshes without any out of tolerance repeats seen in console log. Most conservative would be to leave sample count at 2, but I am having good success rate printing with just 1 sample per location with my speed and distance settings. 

# 5. Leveling Blocks
Use whatever whatever SOLID, same height objects you have for initial setup, but
once you have permanent leveling blocks installed, redo your bed screws adjust and "tune" for bed mesh.

Permanent z-leveling blocks by Stew675 is a convenient design. They can be left in place permanently with minimal loss in max vertical printing height. https://www.printables.com/model/1212350-permanent-bed-platform-levelling-blocks-for-the-qi

# 6. Screws_Tilt_Calculate / Bed Left/Right Tramming
Now that we have the Piezo and induction probes optimized with our [smart_effector] and [bed_mesh] changes, we can use the probes to help with bed leveling.

Do the steps in https://github.com/qidi-community/Plus4-Wiki/tree/main/content/Screws-Tilt-Adjust to enable Screws_Tilt_Calculate. It is faster than working with paper or feeler gauges. 

Tim Carroll suggests adding some extra parameters to improve probing in the printer.cfg SCREWS_TILT_CALCULATE macro. He addes probing speed, distance, and increases number of sampling and reports more repeatable probing during screw adjustment. Following his example and using my probing speeds and distances you would change the macro to...

```
[gcode_macro SCREWS_TILT_CALCULATE]
rename_existing: _SCREWS_TILT_CALCULATE_BASE
gcode:
    { action_respond_info("starting screw rotation calculation...") }
    M141 S0 # disable chamber heater (see https://github.com/qidi-community/Plus4-Wiki/tree/main/content/chamber-heater-issue)
    M4031
    G28
    _SCREWS_TILT_CALCULATE_BASE horizontal_move_z=5 sample_retract_dist=8 samples=3
```

I perform Screws_Tilt_Calculate (and bedmeshes) with print bed at 90C because that is my most common print bed temp. Carroll further suggests also setting nozzle at 140C to emulate printer conditions during bedmesh probing. If you typically print hotter, consider doing screw tilt adjust and bedmesh at your elevated bed temp. Doing this at room temp gives a different result than when performed at printing temperature.

NOTE: We already set left front screw to known good piezo pre-tension. LEAVE THAT LEFT FRONT SCREW ALONE and you will tend end up with other three also at reasonable pretension for piezos. Be leary of big adjustments tightening the adjustment knobs more than one full rotation.

Once you complete Screws_Tilt_Calculate, go into Tune section to do bedmesh. If the mesh looks level enough, save it. Otherwise, repeat Screws_Tilt_Calculate.

# 7. Default Bedmesh and Probing Tolerance Check.
Once screws_tilt_calculate has your bed leveled (all four screws indicated as green), go into Fluidd's "tune" to perform bedmesh. Do so with bed at your usual printing temperature. Examine the mesh to see if there are residual tilts to correct. If so, go back and fine adjust bed screws as needed.

Also, pay attention to the console log and watch for out of tolerance retries. If you cannot get the printer to complete bedmeshes without tolerance warnings, go back to step 4 and change probing speed 1 mm/sec slower and increase probing distance by 0.5 mm. Once the printer has been restarted, reheat bed to temp and repeat "tune" for bedmesh again.

Once the printer can complete four bed meshes in a row without out of tolerance reports, you can consider setting probing count down to 1 for more speed.

Don't forget to save a completed bedmesh as the default bedmesh. 

# 8. Make z-offset-user and Stored z_offset Permanently ZERO
I make these permanently zero to avoid the bug that unpredictably changes z-offset.
In the next step, we will store z-offset-internal explicity for the printer. 
That lets us permanently and specify what the printer is using for distance between bed and nozzle during first layer.

See wiki Making Z_offset Permanent for background understanding, but do NOT do the changes presented there. 
https://github.com/qidi-community/Plus4-Wiki/tree/main/content/making-z-offset-permanent

I only follow its instructions for disabling storage of z_offset and for making it zero in saved_variables. 

Do NOT alter smart_effector as described in the wiki (assuming you wisth to follow my way of specifying and storing z-offset)
This is how I do thingsl..

In Saved_variables.cfg 
Make sure that the stored z_offset is zero.

    z_offset = 0

Next, prevent automatic storage of z_offset
Open gcode_macro.cfg

We disable storage of z_offset from PRINT_END and safe_zoffset by commenting out three lines in each of two macros.

```
[gcode_macro PRINT_END]
gcode:
#    {% if printer.gcode_move.homing_origin.z < 0.5 %}
#       SAVE_VARIABLE VARIABLE=z_offset VALUE={printer.gcode_move.homing_origin.z}
#    {% endif %}

[gcode_macro save_zoffset]
gcode:
#    {% if printer.gcode_move.homing_origin.z < 0.5 %}
#       SAVE_VARIABLE VARIABLE=z_offset VALUE={printer.gcode_move.homing_origin.z}
#    {% endif %}

```

# 9. Set Desired Z-offset for 1st Layer.
I set and store z-offset between bed and nozzle directly in the formula that specifies z-offset-internal

Find the section in gcode_macro for get_zoffset

````
[gcode_macro get_zoffset]
gcode:
    TOGGLE_CHAMBER_FAN
    G1 Z10 F600
    Z_VIBRATE
    QIDI_PROBE_PIN_1
    m204 S50
    G4 P500
    probe probe_speed=5 lift_speed=18 samples=5 sample_retract_dist=10 ; Most critical measurement here. So we leave at 5 samples.
    move_subzoffset
    M114
    {% set p=(-0.15 + printer.gcode_move.homing_origin.z)|float %} ; typically constants of -0.12 for PLA,  -0.15 for PETG, -0.20 for PC  work well on my printers. 
    SET_KINEMATIC_POSITION Z={p}
    G1 Z30 F600
    QIDI_PROBE_PIN_2
    m204 S10000
    TOGGLE_CHAMBER_FAN
````

Notice the formula....
       
    {% set p=(-0.15 + printer.gcode_move.homing_origin.z)|float %}

The -0.15 means the bed should be placed 0.15 mm below z_nozzle_touch for first print layer.

-0.10 would be closer to nozzle

-0.20 would be farther away from nozzle

Recall that thse distance measurements are being performed by printer using the induction probe. Higher temps tend to make induction probes trigger at a shorter distance. So, consider setting bed a little further below nozzle if printing is going to be with high temp filaments. 

Save and Restart for changs to take place.

You will need to experiment to determine your best offset. One way is to manually tweak z-0ffset while printing. Then, remember that value and use that to adjust your formula value.

Each of my printers does best with a slightly different formula z-offset-internal, but they are between -0.12 and -0.15 for my four Plus4 printers despite printing a range for filaments from PLA (205c nozzle / 60c bed) to Polycarbonate (325c nozzle / 115c bed)

=========================

This concludes the changes I make for better piezo and induction probe performance.

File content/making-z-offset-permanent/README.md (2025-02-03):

# Making Z Offset Permanent

## The issue

The Qidi Plus 4 has automatic Z-offset detection, however sometimes the offset that it decides upon may not be quite right.

If we print a large single layer sheet, we can adjust the Z offset on the printer's display screen until we observe that the first layer is going down properly.

This new z offset value is saved to the `saved_variables.cfg` file under the `z_offset` field.

Under certain operations this offset value can be reset back to 0, possibly causing first layer issues once again until set again until we set back to the appropriate value.

The operations that cause the z offset to be reset is not yet completely understood at this moment.

## The Permanent Fix

The way to permanently apply a Z offset value is to add it to the `[smart_effector]` section in the `printer.cfg` file.

As an example, on my printer I determined that an appropriate `z_offset` was 0.04mm as configured on the printer's display screen.

To set this offset permanently, change the sign of the value (eg. 0.04 becomes -0.04, or -0.05 would become 0.05) and copy that value into the `z_offset` field under the `smart_effector` section in the `printer.cfg` file.

An example of this is the following:

```
[smart_effector]
pin:U_1:PC1
recovery_time:0
x_offset: 25
y_offset: 1.3
z_offset: -0.04
speed:5
lift_speed:5
probe_accel:50
samples: 2
samples_result: submaxmin
sample_retract_dist: 5
samples_tolerance: 0.05
samples_tolerance_retries:5
```

After applying this offset value and saving the updated `printer.cfg` file, we MUST edit `saved_variables.cfg` file and set `z_offset` there back to 0.

Ignore all the other values there.

For example:

```
[Variables]
bed_temp = 75.0
file_path = '/home/mks/gcode_files/.cache/3DBenchy.gcode'
filepath = ''
gcode_lines = 50
hot_temp = 0.0
last_file = ''
power_resume_z = 58.0
print_temp = 240.0
profile_name = 'kamp'
was_interrupted = False
z_offset = 0.0
```

## Fixing `gcode_macro.cfg`

Additionally, we need to change the `PRINT_END` and `save_zoffset` macros in the `gcode_macro.cfg` file.

Open up your `gcode_macro.cfg` file, and find the `PRINT_END` macro and comment out the lines as in the below example

```
[gcode_macro PRINT_END]
gcode:
#    {% if printer.gcode_move.homing_origin.z < 0.5 %}
#       SAVE_VARIABLE VARIABLE=z_offset VALUE={printer.gcode_move.homing_origin.z}
#    {% endif %}
```

This prevents the macro from writing over the stored 0 value in `saved_variables.cfg`

We also need to do the same thing in the following `save_zoffset` macro (also in `gcode_macro.cfg`)

```
[gcode_macro save_zoffset]
gcode:
#    {% if printer.gcode_move.homing_origin.z < 0.5 %}
#       SAVE_VARIABLE VARIABLE=z_offset VALUE={printer.gcode_move.homing_origin.z}
#    {% endif %}
```

Just comment out those 3 lines

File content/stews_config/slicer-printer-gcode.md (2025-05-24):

# Slicer Side Printer Gcode

Here's my slicer-side printer start/end/layer change gcode to match my printer config

It should be noted that if you are still running `xindi` (if you don't know what that is,
then the answer to that question for you is **YES**), then **DO NOT** call `PRINT_END` from
the end print macro gcode as `xindi` will do that for you automatically.





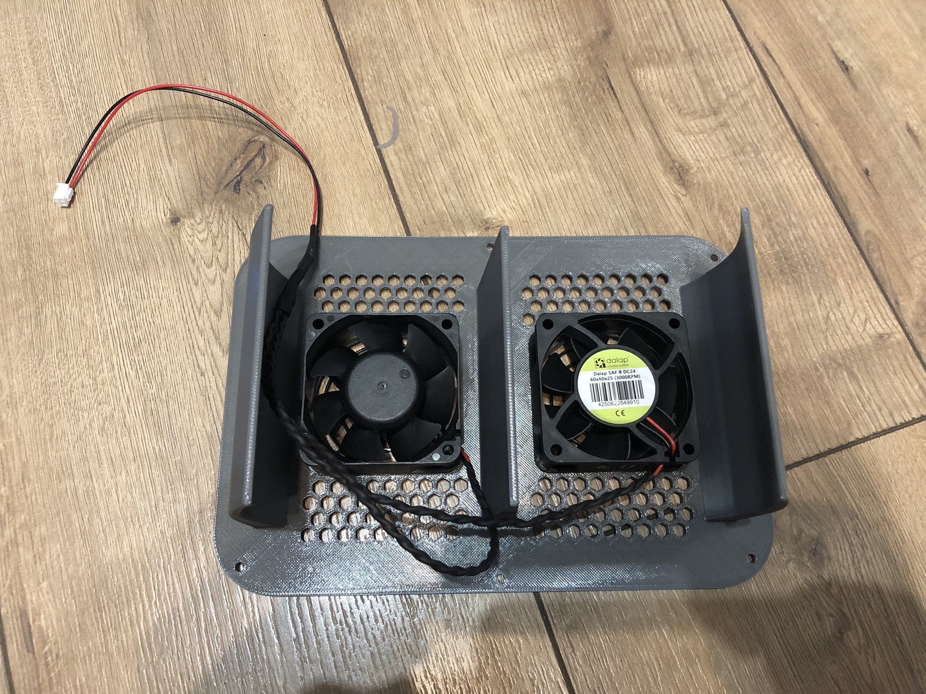
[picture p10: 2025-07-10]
content/mainboard-cooling/img/assembled_back.JPEG

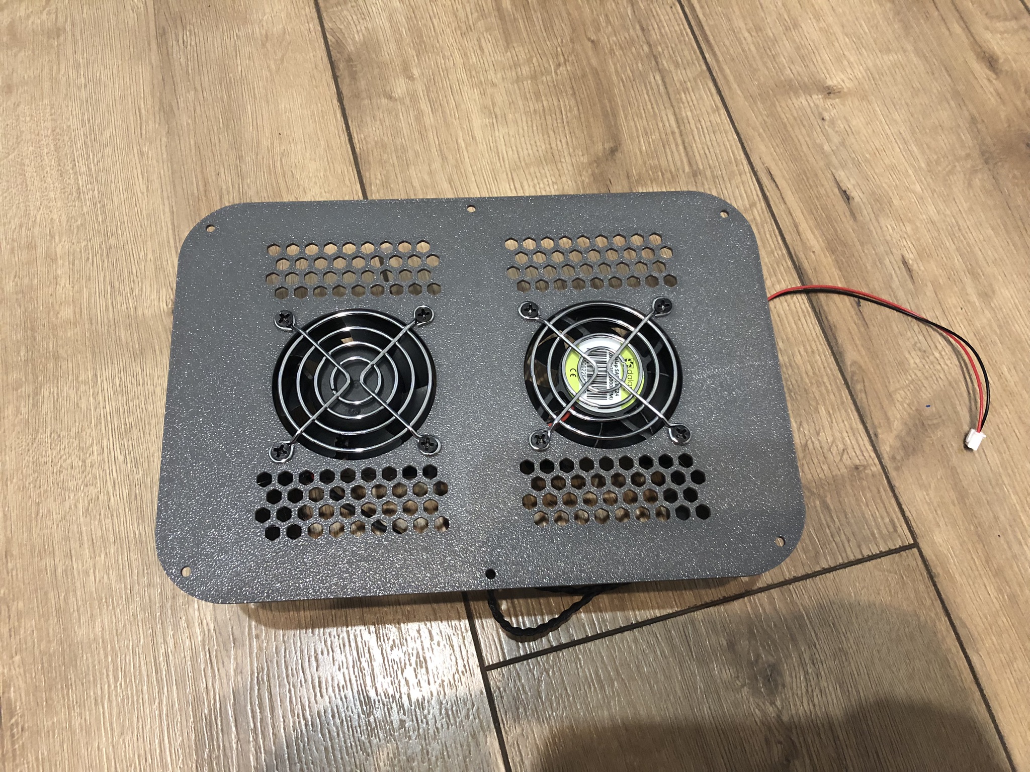
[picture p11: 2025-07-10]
content/mainboard-cooling/img/assembled_front.JPEG

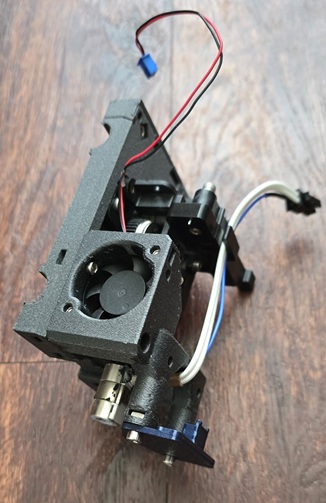
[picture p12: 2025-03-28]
content/modular-toolhead/small/Classic-Beacon-Mount-Assembly-2.jpg

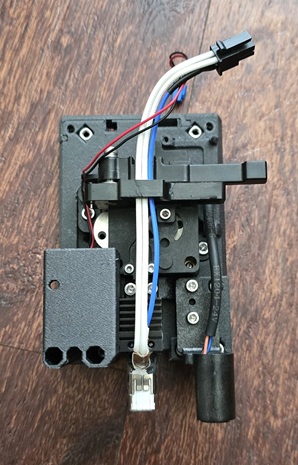
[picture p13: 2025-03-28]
content/modular-toolhead/small/Stock-Fan-Probe-Assembly-1.jpg

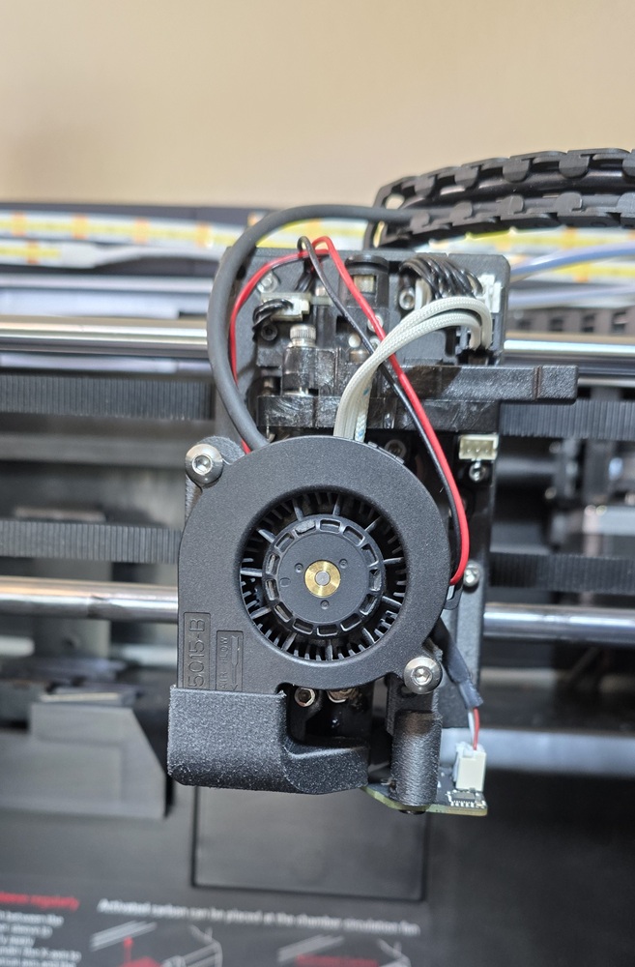
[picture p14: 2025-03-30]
content/modular-toolhead/front-blower-assembly/026.jpg

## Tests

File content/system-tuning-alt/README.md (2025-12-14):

> [!INFO]
> This tuning method is an alternative to [Qidi Plus4 System Tuning](/content/system-tuning/README.md):
> 1. It doesn't use IRQ remapping, which doesn't play a significant role on a modern kernel.
> 2. It's a different method for setting process priorities.
> 3. Only the xindi process requires kernel affinity; everything else is adequately scheduled by the scheduler without significant losses.

# Qidi Plus4 System Tuning - Alternative version

Sometimes you may encounter the following error on your printer:
> MCU 'mcu' shutdown: Timer too close

These errors are caused by a delay in data processing between the MCU and the Klipper process.
The printer has a fairly wide data bus and powerful MCUs.
The problem persists with Klipper - it simply doesn't have enough resources to operate.

> [!IMPORTANT]
> There are many other causes for the "MCU shutdown" error.
> For example, "Lost communication with MCU" is most often a cable issue or a static shock from the filament.
> This article only addresses the "Timer too close" software error.

## Process priority

The newer process scheduling mechanism (cgroup CPU weight, default - 100) will be used to specify processor priority, rather than nice.
Parameters will be specified as a service file extension (systemd drop-in).

The xindi process jumps between processors extremely frequently and will be bound to the last core. It will also be assigned a per-core load quota. This will cause lag when using the screen (especially when loading images), but will prevent it from rapidly consuming all resources.

```shell
sudo mkdir -p /etc/systemd/system/klipper.service.d/ /etc/systemd/system/makerbase-client.service.d/ /etc/systemd/system/moonraker.service.d/ /etc/systemd/system/webcamd.service.d/
echo -e "[Service]\nCPUWeight=700" | sudo tee /etc/systemd/system/klipper.service.d/override.conf
echo -e "[Service]\nCPUWeight=80" | sudo tee /etc/systemd/system/moonraker.service.d/override.conf
echo -e "[Service]\nCPUWeight=10" | sudo tee /etc/systemd/system/webcamd.service.d/override.conf
echo -e "[Service]\nCPUWeight=10\nCPUQuota=25%\nCPUAffinity=3" | sudo tee /etc/systemd/system/makerbase-client.service.d/override.conf
sudo systemctl daemon-reload
sudo systemctl restart klipper makerbase-client moonraker webcamd
```

## CPU Frequency

> [!WARNING]
> Important - all changes from now on are at your own risk.

> [!WARNING]
> Start with good board cooling. You need better cooling!

For some reason, Qidi uses dtb files (similar to BIOS settings) with a frequency limit of 1.2 GHz. However, there is an Armbian dtb file with a frequency of ~1.3 GHz and a slightly higher voltage:

| Frequency | Qidi uV | Armbian uV |
|---|---|---|
| 408MGz | 950000 | 950000 |
| 600MGz | 950000 | 950000 |
| 816MGz | 1000000 | 1050000 |
| 1008MGz | 1100000 | 1150000 |
| 1200MGz | 1275000 | 1225000 |
| 1296MGz | Disabled  | 1300000 |

There are also differences in RAM voltage - a little less in Armbian.

If you have good cooling, you can slightly overclock the SOC:

```shell
sudo cp /boot/extlinux/extlinux.conf /root/extlinux-orig.conf
test -e /boot/dtb-5.16.20-rockchip64/rockchip/rk3328-roc-cc.dtb  && sudo sed -i 's|\(\s*fdt\s\).*|\1/dtb-5.16.20-rockchip64/rockchip/rk3328-roc-cc.dtb|' /boot/extlinux/extlinux.conf
```

Just in case, let's comment out the maximum frequency limit for cpufrequtils (although mine was already ~1.3GHz out of the box):

```shell
sudo sed -i 's/^[^#]*\s*MAX_SPEED=/#&/' /etc/default/cpufrequtils
```

You'll need to power cycle the printer to apply the settings. After powering up, the output will show:

```shell
/usr/bin/cpufreq-info -c 0
```

You should see a frequency of 1.30 GHz. For example:

```
  current CPU frequency is 1.30 GHz (asserted by call to hardware).
  cpufreq stats: 408 MHz:0.00%, 600 MHz:9.10%, 816 MHz:0.00%, 1.01 GHz:0.00%, 1.20 GHz:0.00%, 1.30 GHz:90.90%  (87511)
```

## Uninstall

To disable priority, simply delete the drop-in files:

```shell
sudo rm -v /etc/systemd/system/klipper.service.d/override.conf /etc/systemd/system/makerbase-client.service.d/override.conf /etc/systemd/system/moonraker.service.d/override.conf /etc/systemd/system/webcamd.service.d/override.conf
sudo systemctl daemon-reload
sudo systemctl restart klipper makerbase-client moonraker webcamd
```

To disable overclocking, run the following command and power cycle the printer:

```shell
test -e /boot/dtb/rockchip/rk3328-roc-cc.dtb && sudo sed -i 's|\(\s*fdt\s\).*|\1/dtb/rockchip/rk3328-roc-cc.dtb|' /boot/extlinux/extlinux.conf
```

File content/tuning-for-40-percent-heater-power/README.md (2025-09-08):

# Tuning Chamber Heater Warmup Times

## Introduction

> [!CAUTION]
> For firmware v1.6.0 or later, you have two choices:
> 1. Don't use this warmup sequence at all.
> 2. Use the [Improved PRINT_START macro](#Improved-PRINT_START-macro) in addition to the steps detailed in [Firmware v1.6.0 - Required Steps](#firmware-v160---required-steps).

***

With the 1.4.3 Firmware Release from Qidi, the stock chamber heater power was dropped from a 70% duty cycle to a 40% duty cycle.

This now made chamber warmup times considerably slower as a result, however we can make some configuration changes to make it not so bad.

Now keep in mind that the primary point of slowness during a print start warmup was actually the print bed, and not the chamber heater warmup,
and we can use this to our advantage to improve the overall situation.

## Test Baseline

### Initial Conditions

- Room Temperature: 23C
- Starting Chamber Temperature: 23C
- Starting Print Bed Temperature: 23C

### Target Conditions

- Chamber: 60C
- Print Bed: 100C

### What are we measuring here?

It makes the most sense to measure the time elapsed between when a print is sent to the printer,
and the time when the bed meshing starts for the print.  This really is the only time that matters here.

## Test 1 - Warmup times at 70% heater power

It was observed that while the chamber temperature would reach the target within 10 minutes,
the print bed would only reach 100C after 16 minutes and 30 seconds before the bed mesh started.

## Test 2 - Warmup times at 40% heater power, stock configuration

It was observed that it took 25 minutes to the time that the bed meshing started

## Test 3 - Warmup times at 40% heater power with tuned `PRINT_START` and `M191` macros

A time of 19m30s was observed to the time that the bed meshing started.

## Improved PRINT_START macro

Change the `PRINT_START` macro within `gcode_macro.cfg` to the following in its entirety.
I've added detailed comments to (almost) every line so it is easier to understand what all
the gcode is doing.

**Note:** I recommend just commenting out the stock `PRINT_START` macro by putting a
`#` at the start of all of the original macro lines.
Then copy-paste this new macro in either before or after the original macro.
This will allow you to easily revert to the original macro should you wish to do so.

```
[gcode_macro PRINT_START]
gcode:
    {% set bedtemp = params.BED|int %}
    {% set hotendtemp = params.HOTEND|int %}
    {% set chambertemp = params.CHAMBER|default(0)|int %}

    # AUTOTUNE_SHAPERS                  # Nothing ever makes uses of this though
    # set_zoffset                       # Sample the Z offset (but why even do this now?)
    M141 S{chambertemp}                 # Initiate Chamber Warmup as early as possible
    M140 S{bedtemp}                     # Initiate Print Bed Warmup as early as possible
    M400                                # Wait for all prior G-code commands to be processed by MCU
    M104 S0                             # Make sure hotend is off
    M106 P3 S0                          # Turn off chamber circulation/exhaust fan
    M106 S0                             # Turn off part cooling fan

    {% if chambertemp > 0 %}
        M106 P2 S255                    # Set AUX to full to help mix chamber air fully
    {% else %}
        M106 P2 S0                      # Turn off auxiliary part cooling fan
    {% endif %}

    M400                                # Wait for all prior G-code commands to processed before G28
    G28                                 # Home all axes
    CLEAR_NOZZLE HOTEND={hotendtemp}    # Do nozzle purge and wipe

    {% if chambertemp > 0 %}            # Special chamber handling for fastest thorough warmup times
        M106 P0 S255                    # Ensure part cooling fan is full speed for better air mixing
        M106 P2 S255                    # Ensure AUX is at 100% after CLEAR_NOZZLE was called
        G0 Z5 F600                      # Bring print bed to Z=5mm.  This helps with chamber heating
        G0 X152 Y152 F6000              # Bring print head to middle of print bed
        M191 S{chambertemp-5}           # Wait for chamber to reach 5C less than the target temperature
        M141 S{chambertemp}             # Reset chamber target to full target
        M106 P2 S0                      # Turn off AUX Fan
        M106 P0 S0                      # Turn off part cooling fan
    {% endif %}

    G0 X5 Y5 F6000                      # Move print head to front-left in case of any oozing
    M104 S140                           # Set nozzle to 140 so any remaining filament stuck to nozzle is softened
    M190 S{bedtemp}                     # Wait for print bed to reach target temperature
    G29                                 # Perform Z-offset, and bed meshing measurements
    M104 S0                             # Ensure hotend is fully off to minimise any oozing

    {% if chambertemp == 0 %}           # No chamber temp set. This means we're likely printing PLA/PETG.
        M106 P3 S255                    # Set the chamber circulation fan to 100% to minimise heat creep
    {% endif %}

    G0 Z5 F600                          # Move plate to Z=5mm
    G0 X5 Y5 F6000                      # Move print head to front-left
    M141 S{chambertemp}                 # Ensure chamber is set to on after G29 was called earlier
    M109 S{hotendtemp}                  # Commence hotend warmup
    M204 S10000                         # Set velocity limits
    SET_PRINT_STATS_INFO CURRENT_LAYER=1
    ENABLE_ALL_SENSOR
    save_last_file
```

Additionally, in `printer.cfg` find the `[verify_heater heater_bed]` section, and change the `check_gain_time` from `60` to `360` as in the following example.
This is required because the print bed is being blasted by the fan to heat the air up faster, which means that the print bed itself heats
up more slowly.  If we don't raise this check gain time a bit, then the firmware may throw an error because it is not seeing the print
bed warm up quickly enough.

```
[verify_heater heater_bed]
max_error: 200
check_gain_time:360
hysteresis: 10
heating_gain: 1
```

### Discussion on why it works

- Some needless commands were commented out, but left in place if ever needed at a future time.
- The print bed is raised up and the auxiliary fan and print head fans are used to transfer as much heat from the print bed to the chamber air as possible
- This is basically using the print bed's heater to its fullest effect to boost the chamber heater in warming the chamber air
- The `M191` chamber wait target is lowered to 5C less than the true target meaning the chamber wait ends a bit sooner
- While Z-offset and bed-meshing takes place, the chamber continues to warm up to the target in the meantime
- The chamber is observed to be fully up to temperature by the time the actual print begins

### Additional Notes

It is **absolutely essential** that the `Activate Temperature Control` option is disabled in the filament settings in your slicer.
If this feature is active, then the slicer will instruct the printer to attempt to warm the chamber without the assistance of the print bed heater,
and there are reports that this can take up to 1 hour for the chamber to reach 60C.

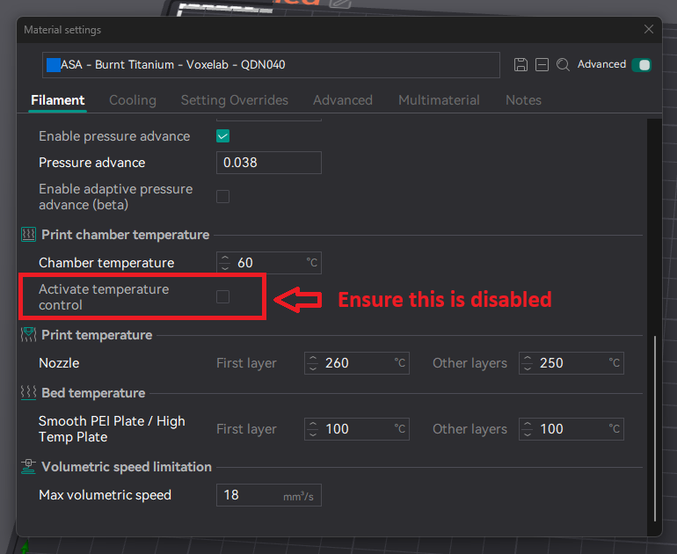
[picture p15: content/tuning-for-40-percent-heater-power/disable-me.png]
DISABLE THIS! You REALLY don't want this enabled!


## Firmware v1.6.0 - Required Steps

> [!CAUTION]
> Do not follow these steps if on firmware earlier than v1.6.0 !!

### Modifying heaters.py

### SSH into the printer

SSH into your printer as specified [here](https://github.com/qidi-community/Plus4-Wiki/blob/main/content/ssh-access/README.md).

#### 2. Automatic patching
You may use our automatic patching script. You can download it on your printer as such:
```bash
wget https://github.com/qidi-community/Plus4-Wiki/raw/refs/heads/main/content/tuning-for-40-percent-heater-power/auto-heaters-patch.sh -O /tmp/auto-heaters-patch.sh
```
and then execute it as such:
```bash
bash /tmp/auto-heaters-patch.sh
```

If everything worked correctly, you should see the script outputting `Patch applied successfully!`.

If so, you can skip Step 2bis.
Else, you can try manual patching.

#### 2bis. Manual patching
This is step should be done, if the previous automatic patching failed.
If the automatic patch failed, you may instead patch your heaters.py manually as such:

1. Write a new file named `heaters.patch` with these contents:
<details open>
<summary>Patch for heaters.py</summary>

```patch
--- a/klippy/extras/heaters.py
+++ b/klippy/extras/heaters.py
@@ -234,7 +234,10 @@ class ControlPID:
         #logging.debug("pid: %f@%.3f -> diff=%f deriv=%f err=%f integ=%f co=%d",
         #    temp, read_time, temp_diff, temp_deriv, temp_err, temp_integ, co)
         bounded_co = max(0., min(self.heater_max_power, co))
-        if self.heater.name == "chamber" and heater_bed.heater_bed_state != 2 and heater_bed.is_heater_bed == 1:
+        # We add this DISABLE_BED_CHECK flag so that the chamber heater can be controlled independently of the bed heater
+        # This should not be used in normal operation with the stock piezo sensor
+        DISABLE_BED_CHECK = True
+        if self.heater.name == "chamber" and heater_bed.heater_bed_state != 2 and heater_bed.is_heater_bed == 1 and not DISABLE_BED_CHECK:
             self.heater.set_pwm(read_time, 0.)
         else:
             self.heater.set_pwm(read_time, bounded_co)
-- 
```

</details>

2. Apply the patch 
```
patch /home/mks/klipper/klippy/extras/heaters.py < /path/to/heaters.patch
```

3. If that was successful you will see something like `patching file heaters.py` without any further output and an exitcode of `0` (execute `echo $?`, which is the exitcode of the last executed command).



### Explanation

We have modified the code in heaters.py to add a `DISABLE_BED_CHECK = True` flag. 
Where normally the chamber heater does not turn on unless the bed is within 2 degrees of the target bed temp, we ignore this using our new flag.

Set `DISABLE_BED_CHECK = False` if you want to revert to the default behavior.

```python
        # We add this DISABLE_BED_CHECK flag so that the chamber heater can be controlled independently of the bed heater
        # This should not be used in normal operation with the stock piezo sensor
        DISABLE_BED_CHECK = True
        if self.heater.name == "chamber" and heater_bed.heater_bed_state != 2 and heater_bed.is_heater_bed == 1 and not DISABLE_BED_CHECK:
            self.heater.set_pwm(read_time, 0.)
        else:
            self.heater.set_pwm(read_time, bounded_co)
        # Store state for next measurement
        self.prev_temp = temp
        self.prev_temp_time = read_time
        self.prev_temp_deriv = temp_deriv
        if co == bounded_co:
            self.prev_temp_integ = temp_integ
        if self.heater.name == "heater_bed" :
            if target_temp < 70:
                heater_bed.heater_bed_state = 0
            elif temp < target_temp - 2.:
                heater_bed.heater_bed_state = 1
            else:
                heater_bed.heater_bed_state = 2
```
## Restart the Printer

> [!NOTE]
> If you've edited the files through Fluidd, Use the orange "Save & Restart" button up top

The files we've just edited are not necessarily written to disk yet. To force this to happen, run the command `sync`.   
If `sync` comes back with no further remarks and patching was successful, you can powercycle the printer.   



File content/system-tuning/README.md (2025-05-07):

> [!IMPORTANT]
> The original version of the tuning script had a compatibility issue with `xindi`.  This has now been resolved. Please re-download and apply the updated tuning script if you installed a version prior to 8th Jan 2025.

# Qidi Plus4 System Tuning

If you've ever encountered the following error, or just want to make your Plus4 a little more responsive overall, this is the page for you.

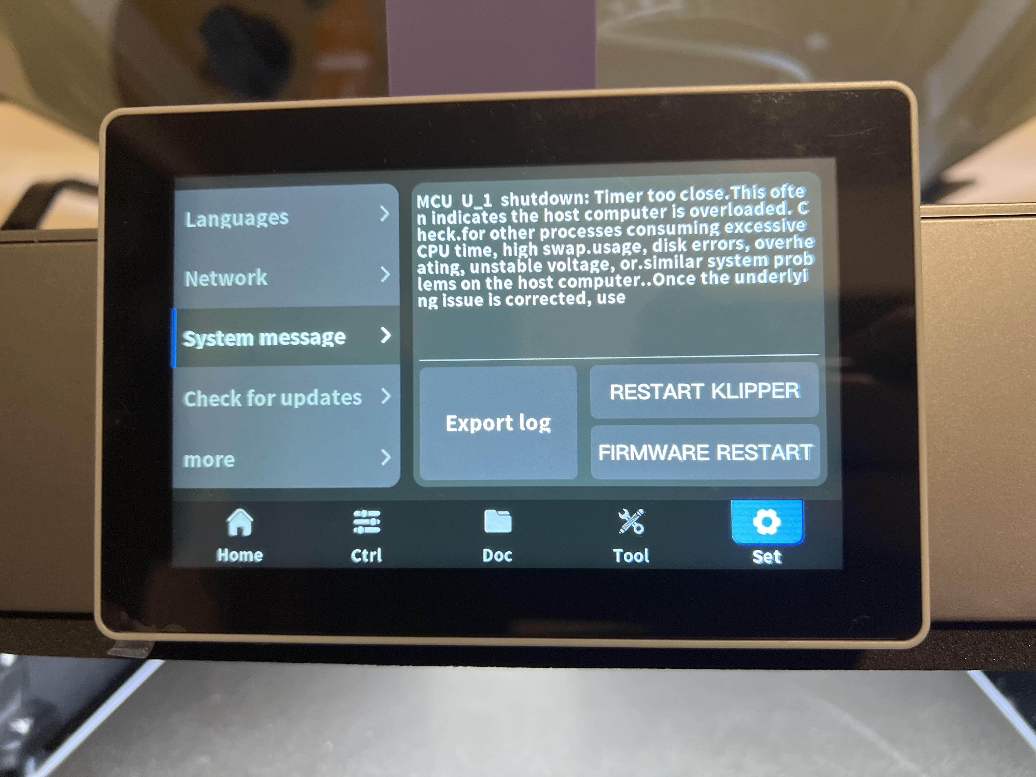
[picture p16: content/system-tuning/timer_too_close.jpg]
Timer Too Close It's too close!


## Introduction

The Qidi Plus4 utilises a RockChip based CPU with 4 cores running at a peak of 1.2Ghz

As such, there can be instances under certain high loads where the CPU can struggle to keep up with the MCU systems controlling the motion systems,
which leads to the occasional "MCU: Timer Too Close" (TCC in short) errors that causes Klipper to shut down.

There are a number of CPU intensive processes that can compete with Klipper for CPU resources

- `xindi` is Qidi's UI interface driving daemon that is responsible for converting clicks on the printer screen into Klipper actions, as well as driving USB storage, networking, and firmware updates
- `mjpg_streamer` is the video streaming encoding daemon that provides a video stream to monitor the current print
- `nginx` is the Web Server daemon that hosts the FluiddUI Web Interface service that slicers and a web browser can interact with
- `moonraker` is the API process that acts as an intermediary between Klipper and Web UI's such as Fluidd or Mainsail

Unfortunately the above processes can sometimes get in the way of Klipper, and cause CPU stuttering that is bad enough to cause TCC errors.

Additionally, the CPU is configured to run in an on-demand frequency-scaling mode that can also introduce stuttering as the Linux scheduler tries to dynamically adjust the CPU frequency to respond to high load scenarios.

Fortunately there are ways in which we can tune Qidi's system to better optimise the CPU power mode and resource usage.

## Installing a run-time system tuning script

I have developed a run-time service script that attempts to isolate non-Klipper essential services to an individual CPU core
as well as bind Klipper services the remaining 3 CPU cores.

Additionally, the CPU is placed into performance mode to prevent it from scaling its frequencies when idle.  This allows it
to respond more quickly to the load spikes that Klipper can introduce.

While ideally this installation procedure should be run when not printing anything, it is not a requirement.  It is generally safe
to install and run this script at any time.

## Installing the Tuning Script

To install and activate the tuning, follow this sequence of steps:

1. ssh into your 3D Printer's Linux command shell (see [ssh-access](https://github.com/qidi-community/Plus4-Wiki/tree/main/content/ssh-access) for details)

2. Obtain a root shell on your printer like so:

```
sudo bash
```

3. Now run the following commands:

```
wget -O - https://raw.githubusercontent.com/qidi-community/Plus4-Wiki/refs/heads/main/content/system-tuning/tuning > /etc/init.d/tuning
chmod 755 /etc/init.d/tuning
ln -sf /etc/init.d/tuning /etc/rc3.d/S99tuning
/etc/init.d/tuning reload
```

This installs the tuning script and sets it up to run at system startup when the printer is powered on
It also does a one-time system tuneup for the currently running system so there's no need to power-cycle your printer.

> [!NOTE]
> `mjpg_streamer` often creates transient short-lived threads, and so the script may occasionally complain that it cannot find one of the `mjpg_streamer` processes.  In the chance that this error is seen, then it can be safely ignored.

4. Now exit out of the root shell like so with the following command:

```
exit
```

## Verifying CPU Performance Mode

Run the following command:

```
/usr/bin/cpufreq-info -c 0
```

This should generate output similar to the following:

```
cpufrequtils 008: cpufreq-info (C) Dominik Brodowski 2004-2009
Report errors and bugs to cpufreq@vger.kernel.org, please.
analyzing CPU 0:
  driver: cpufreq-dt
  CPUs which run at the same hardware frequency: 0 1 2 3
  CPUs which need to have their frequency coordinated by software: 0 1 2 3
  maximum transition latency: 62.0 us.
  hardware limits: 408 MHz - 1.20 GHz
  available frequency steps: 408 MHz, 600 MHz, 816 MHz, 1.01 GHz, 1.20 GHz
  available cpufreq governors: conservative, ondemand, userspace, powersave, performance, schedutil
  current policy: frequency should be within 1.20 GHz and 1.20 GHz.
                  The governor "performance" may decide which speed to use
                  within this range.
  current CPU frequency is 1.20 GHz (asserted by call to hardware).
  cpufreq stats: 408 MHz:0.00%, 600 MHz:0.03%, 816 MHz:0.00%, 1.01 GHz:0.00%, 1.20 GHz:99.96%  (520)
```

The important lines here at the 3 lines starting at `current_policy:`

The above output is informing us that the CPU will choose a frequency between 1200MHz and 1200Mhz (ie. a constant 1200Mhz) and that the `performance` CPU frequency governor is active.

This verifies that the CPU on the Plus4 is now operating in its highest possible performance mode.

## Verifying Process Niceness

When you first ran `/etc/init.d/tuning reload` there would have been a lot of diagnostic output explaining what the script was doing.
You should see that all `xindi` was affined to CPU 0, that `mjpg_streamer`, `moonraker`, and `nginx` processes and threads were affined to CPU 3, and all
`klippy` processes and threads were affined to CPU 1 and 2.



To verify the Unix scheduling niceness changes run the `top` command and take note of the nice level for the `xindi`, `mjpg_streamer`,
and `nginx` processes (in the `NI` column). The values should be set to `1`, `2`, and `1` respectively.  The script does not adjust the niceness level of
either `klippy` or `moonraker` (ie. the `python` commands and line 2 and 3 of the screenshot) so their nice levels should remain at `0`.



Alternately, run the following command:

```
ps axl | egrep "mjpg|xindi|nginx" | egrep -v "bash|grep" | awk '{print $6 " " $13}'
```

and that will extract the Nice level of the processes, and should present output similar to the following:

```
2 ./mjpg_streamer
1 /root/xindi/build/xindi
1 nginx:
1 nginx:
1 nginx:
1 nginx:
1 nginx:
```

where the number at the start represents the Nice level of the process

## What if I restart `mjpg_streamer` by changing values in `webcam.txt`?

In the event that you modify the `webcam.txt` parameters, this will intiate a new set of `mjpg_streamer` process/threads
and the tuning script will need to be manually re-run if you don't wish to power-cycle the printer.  This can be achieved
at any time with the following command:

```
sudo /etc/init.d/tuning reload
```

which will re-apply the tuning to the currently running system

## Deactivating the Tuning

If you wish to deactivate the system performance tuning, without uninstalling the script, run the following command:

```
sudo /etc/init.d/tuning stop
```

This can be useful when making comparisons as to how the printer behaves with, and without, the tuning parameters active

## Uninstalling

In the event that the tuning script is causing any issues, it can be uninstalled via the following procedure:

Log into your printer via ssh and run the following command:

```
sudo /etc/init.d/tuning stop
sudo rm -f /etc/init.d/tuning /etc/rc6.d/S99tuning
```

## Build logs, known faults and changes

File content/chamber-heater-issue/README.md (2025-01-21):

# Chamber Heater Issue

## Description

This problem only affects **prints taller than 268mm** when printing with materials that require the chamber heater to be enabled.

The hot air exhaust of the chamber heater exits into the main chamber towards the very bottom of the left side of the chamber.

Unfortunately the print bed, when at Z heights of 268mm and greater will increasingly block off the chamber heater's outlet when the heater is active.
This can lead to a thermal event being triggered by Klipper, resulting in Klipper shutting the firmware down immediately and ruining any print in progress.

A true fix for this issue would require Qidi to come up with a hardware fix that does not result in the print bed blocking the outlet of the chamber heater when the print bed is near the very bottom of the chamber.

## A firmware configuration workaround

**NOTE:**  While the following does not fix the fundamental hardware flaw in the printer's design, it does essentially nullify its impact.

The following configuration will disable the chamber heater's coils whenever the print bed is at a Z height of 268mm or greater.
The idea here is to disable the heater coils and then complete the remainder of the print using the latent heat within the chamber **and** by making best possible use of the heating element of the print bed.
This will mitigate the firmware shutdown issue and, in almost all reasonable scenarios, will allow the print to complete successfully.

Within the `gcode-macro.cfg` file we can add in the following macro:

```

[gcode_macro SET_PRINT_STATS_INFO]
rename_existing: SET_PRINT_STATS_INFO_BASE
gcode:
    {% set curlayer =  params.CURRENT_LAYER|default(1)|int %}
    {% if (printer.toolhead.position.z) >= 268 %}
        # Set chamber target to 10C, which still keeps the chamber heater fan on
        # This allows the print bed to warm the chamber more effectively even
        # though the heater coils are effectively disabled
        M141 S10
    {% endif %}
    SET_PRINT_STATS_INFO_BASE CURRENT_LAYER={curlayer}

```

This will call the macro upon every layer change (as this command is called on every layer change in all stock printing profiles).
When the Z height exceeds 268mm, the chamber heater target will be set to 10C.

**The target of 10C is important here, instead of using a 0C target.**

Using a 10C target will keep the chamber heater's fan spinning, which will still help to circulate some air under the print bed,
and this will in turn help to keep the chamber warm as the print bed warms the air-flow under it.

Doing this will prevent the chance for a thermal shutdown event being triggered by the chamber heater, and will keep the chamber warm for the remainder of the print.

## IMPORTANT UPDATE FOR v1.6.0 FIRMWARE

The v1.6.0 firmware introduces a new field called `target_min_temp` to the `[heater_generic chamber]` config section.  The above
macro conflicts with this new field unless `target_min_temp` is set to 10

For example:

```
[heater_generic chamber]
heater_pin:U_1:PC8
max_power:0.4
sensor_type:NTC 100K MGB18-104F39050L32
sensor_pin:U_1:PA1
control = pid
pid_Kp=63.418
pid_Ki=1.342
pid_Kd=749.125
min_temp:-100
max_temp:70
target_min_temp: 10            #<--- Ensure that this field is set to 10C (default is 45C)
target_max_temp:65
heat_with_heater_bed:True
heat_with_heater_bed_tem_add:25
```

## Additional Safety Configurations

### Setting the chamber_fan shutdown_speed

In addtion, for added safety the chamber heater fan can be set to run even if the printer does shut down due to the chamber heater overheating.
This can be done by modifying the following in `printer.cfg`:

```
[chamber_fan chamber_fan]
shutdown_speed: 1 
```

### Setting the chamber_heater power to 0.4 (instead of 0.7)

Qidi's stock PWM power setting for the chamber heater for Firmware versions 1.4.2 and earlier is too aggressive and has been known to cause
the Chamber Thermal Protection Sensor to trip.
This has been seen to result in a firmware shutdown even in normal operation when a print is first starting to warm the chamber up.

Making the following config change will prevent this from happening.

Additionally, setting a lower `max_power` value here will also help protect the SSR unit from potentially failing in 110VAC countries as reports
of this for the first batch of Plus4 printers have started to surface somewhat frequently within the first month of customer use.

Find the `[heater_generic chamber]` section within the `printer.cfg` file, and then find the line starting with `max_power`, and set its value to `0.4`.

For example:
```
[heater_generic chamber]
max_power:0.7
```

Should be replaced with:

```
[heater_generic chamber]
max_power: 0.4
```

Note that while the chamber will take a little longer to reach a target temperature, it should still reach the target temperature before
the print bed reaches it own target in almost all reasonable scenarios.

**Additional note!!!**

This should actually be standard from Qidi, but it's not:

Within the `G29` macro, which is normally located in the `gcode_macro.cfg` file, find that macro, and change the `M141 S0` portion
at the start of the macro to the following:

```
[gcode_macro G29]
variable_k:1
gcode:
    {% set temp = printer["heater_generic chamber"].target %}
    M141 S0
    {% if temp > 0 %}        # ADD THESE
        G4 P15000            # 3 EXTRA
    {% endif %}              # LINES HERE
    BED_MESH_CLEAR
    ...                      # Rest of macro continues as before
```

This will ensure that the chamber fan will stay on for at least 15 seconds longer to allow for the heater unit
to cool down a little more before `get_zoffset` turns the chamber fan off with `TOGGLE_CHAMBER_FAN` after `G28` is called.

Ideally, Qidi should not be disabling the chamber fan on a potentially hot heater unit, so this is the best we can do in the
meantime until they fix this bit of ugliness.

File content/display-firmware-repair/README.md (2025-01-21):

# So you borked your touchscreen...

If a firmware update went sideways, or the screen just spontaneously decided to die, and now the screen is plain white with "DATA ERROR" in red text on it, or similar, you can fix it with a couple simple steps and a usb flash drive. 

### Step-by-step
1) Get a usb drive that is usable with the printer. One formatted into FAT32 will do, size largely doesn't matter. Usb drive that came with the printer was used in testing.
2) Find out, remember, or guess what printer firmware version you had. Example numbers are 1.3.2, 1.4.3, 1.6.0.
3) Download the firmware update for that version, so if you had 1.6.0 installed, get a 1.6.0 update file. You may also reuse one you already downloaded before.
4) Unpack it, and find a file named `QD_Plus4_UI`, rename it to `mksscreen.recovery`, all lowercase exactly as it's written.
5) Put the now renamed `mksscreen.recovery` file in the "root" of the flashdrive (not into any kind of folder, right onto the flash drive).
6) Turn off the printer (flip the power switch) and wait for 30 seconds.
7) Plug the usb drive you just prepared into the printer, and turn it on. 
8) Sit back and relax for an hour while the printer flashes the screen firmware.
9) Once the printer screen reboots and starts working normally, remove the usb flash drive and delete the `mksscreen.recovery` file from it so the printer won't repeat the flashing process every startup.

### Possible problems encountered: 
#### Issue 1: The printer went back to "DATA ERROR!" screen
Repeat the process from step 6. 
#### Issue 2: The printer displays a qidi UI saying update succeeded, but then complaints about a firmware version mismatch. 
Note down the "SOC: XXXXX" number in the bottom right of the error, this is the version the printer thinks it has. You made a mistake in step 2 and need to find a different update file.
#### Issue 3: The screen says UPDATE FAILED in small red text on white background
The screen is possibly lying. Temporarily remove the usb flash drive and restart the printer at the power plug. It may go to issue number 1 mentioned above.
###4 Issue 4 and later: ??????
If you find more, please open an issue on the project (tab in the github interface), and describe what you're having and steps you've taken. Attach a picture if possible.

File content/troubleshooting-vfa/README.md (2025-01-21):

# Troubleshooting VFAs (vertical fine artifacts)

Before attempting anything in this guide, you should already have your printer setup and tuned. Input shaper must be active and tuned. 

VFAs are usually the last item to tune because all other issues must be ruled out first.

An excellent resource is [Ellis' guide](https://ellis3dp.com/Print-Tuning-Guide/articles/troubleshooting/vfas.html). Much of this article uses advice from his guide.

Which one of these has VFAs?

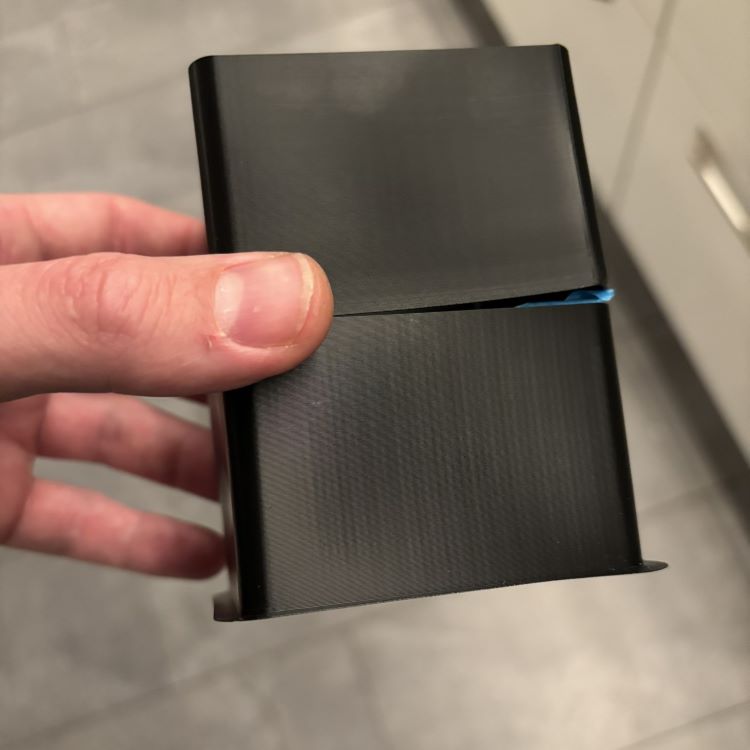
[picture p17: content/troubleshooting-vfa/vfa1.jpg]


(Answer: Both)

Both of these test prints are examples of VFAs. The spacing can vary, they can be faint sometimes, but they are always perfectly vertical.

## Possible solutions

If you confirm you do indeed have VFAs, there are several steps that can be taken to fix them.

### Check belts and pulleys 

Run your finger across all your belts and feel if there is any debris attached to them. Use a cloth to gently wipe off the belts.

Check your idler pulleys are clean and spinning when the belts move. You want all of your pulleys to spin freely without resistance. 

### Tighten belts

Follow [this guide](https://wiki.qidi3d.com/en/Plus4/Maintenance/Adjustment-belt) for tightening the belts. 

If you think your belts are too loose, you can [print a mod](https://www.printables.com/model/1044712-qidi-plus4-belt-tensioners/comments/2134355) which should give you more control over the belt tension. 

### Lube idler pulleys

Follow [this video](https://drive.google.com/file/d/1_KHpMQJNxle0u21L5dIt-LYLbkvVnGiD/view) for how to lube your idler pulleys. 

Your idlers may spin just fine because they could be sticking a tiny bit or they are rubbing on the plastic housing. You can use oil (as demonstrated in th video) or PTFE based grease. 

### Check your X Carriage Screws

If you had the problem with a wobbly X Carriage due to the bearing being loose, check the screws are not too tight. If you do not have the loose bearing issue, do not use the screws.

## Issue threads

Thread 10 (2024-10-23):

Motherboard Fan

kuehmayer, 2024-10-23:
I installed the sunon fan (exactly same as the link, just from amazon) and noticed it only really kicks in at ~99% and struggles to turn below that. Tested it with an external power supply and worked fine. The sunon states 1.2W (0.05A), I measured 0.044A max, and it is starting at 3V (0.012A). For the original it states 0.1A, however, I measured  0.023A max, and it´s starting at 12V ( 0,011A).

So I think the output current to overcome the start up for the sunon is not high enough from the 4 Plus.
Is it working for anyone else or am I doing something wrong?

For now, I´ll adjust the PID settings to start at 0.998 and max 1 haha.

spooknik, 2024-10-24:
Hello!

I think you ended up getting a version of the fan that does not have the ability to do PWM. So it's just either fully on or fully off... can you still return it to Amazon and get something else? [These fans from Anvison](https://www.amazon.com/ANVISION-2-Pack-Brushless-Cooling-Bearing/dp/B0C18G953Z) should do the trick if you're buying from Amazon.

stew675, 2024-10-26:
The Anvision ones that @spooknik linked to are exactly the ones that I use, and I can confirm that they work with the profile as listed.

Closed 2024-10-31.

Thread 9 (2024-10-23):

Screw Sizes?

nicwilson58, 2024-10-23:
Sorry if this is the wrong place to ask this.   the video for the Offical QIDI Toolhead fix video states to use 3*8 self tapping screw.  What size is this,  all the screw sizing in Australia does come in that format so the size of the two screws required escapes me.

thanks
Nic

stew675, 2024-10-23:
I'm fairly certain that they mean any self tapping screw of at least 3mm in diameter, and of 8mm in length.

I think the guy in the video just used standard M3x8mm SHCS screws, and not actually self-tappers.

A 6g screw is 3.5mm in diameter, so that would work too.  I personally used 6g screws myself, of 3/8" (~9.5mm) in length.

Try to use screws that have a flat tip, instead of a sharp pointy tip, or at least file down the tip of any screw you use to be flat.

Since you're in Australia, something like this: https://www.bunnings.com.au/zenith-6g-x-12mm-zinc-plated-pan-head-sheet-metal-screws-100-pack_p2437506

but you only need 2, and file the tips down to be fairly blunt.

I hope that helps.

nicwilson58, 2024-10-23:
thank you for that I found some black,  M3 x 8mm flat screws in my 3d printer kit that look the same as the ones in the video so they should work fine hopefully.

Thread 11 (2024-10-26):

Please confirm new stepper microsteps values

nicwilson58, 2024-10-26:
I am altering my stepper values as you suggested but would like to clarify the stepper_z and stepper_z1

The x and y stepper microsteps were 32 and I have raised them to 64

however my two z values as installed  by firmware 1.43 are both set to 128,  can you please confirm dropping them to 32 as noted in your example.

stew675, 2024-10-26:
Yes, the 32 was intentional.

The Z lead screws have a 4mm thread pitch, meaning the bed travels 4mm for 1 full rotation.

The Z steppers have 200 full steps per full rotation.

The stock config allowed for 128 micro-steps per full step.

Running the math, the size of each micro-step was :  (4.0mm / 200) / 128 ~= 0.00016mm, or 0.16 microns.

That level of resolution simply isn't necessary on the Z axis, nor is it even achievable (with repeatable accuracy) in practice.  The move to 32 steps results in more positionally accurate motions (in a real sense, as opposed to on paper), and at a 0.6 micron resolution, which is still way more than necessary, but it does free up some processing overhead on the MCU to allow it to spend that processing power on better accuracy with the X/Y motions.

Closed 2024-11-15.

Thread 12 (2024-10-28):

Stepper Motor Tweaks Considerations

nicwilson58, 2024-10-28:
When I read the "Stepper Motor Tweaks" changes it seemed like a great idea.  I purchased a very good quality 80mm fan with the same connector so no wiring changes.  I printed the new mount and fitted it.  I then made the changes as recommeded in the "Stepper Motor Tweaks" guide.

Before making the changes and when idle and no board fan running fan running the "host" temperature ranged from 65 - 75c,  so I could see why the fan should be enabled always at a lower speed,  and why you targeted 45c for the host sensor.

After the changes I found the 80mm fan running at 30% could very easily bring the host temperature down to 45c,  and even while printing the host temperature never get above 45c and so the board fan remains at 30% and rarely gets faster and the stepper drivers were easily reaching above 85c (with the new 1.15 current setting)

I made some alterations to check what the stepper temperatures would be  at 100% fan printing the same model.  The stepper temperatures were now between 65 - 69c,  far cooler than before.  I understand we cannot use the 2240 temp sensor to control this, but to me so far it seems the host temperature is also not very suitable.

Of course the findings are for my printer,  others may be different,  buy I am interested in your thoughts around this.
Regards
Nic

jojolll, 2024-11-05:
Hi,

I also agree with you about the cooling of the steppers, which I found insufficient with these tweaks. I kept the original logic where the fan runs at 100% as soon as the steppers are active (and in a few other conditions).

I'm considering adding an idle mode soon, which would leave the fan running at 25%, ensuring that the card still gets cool air even when idle. The steppers, even when off, aren't completely cold, for example, and the CPU heats up too. So, switching off the fan isn't always optimal.

nicwilson58, 2024-11-05:
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

I have already done this,  and found some things.  Many fans I tried are not stable at 25%,  so at idle mine are at 35% which keeps the chipset cool.  Idle does not seem stable also,  the idle timeout is sometimes very rarely called so I dont use it.  use the mcu temp to reduce the fan to 35% when the target temp of 50c is reached,  it then idles at 35% and stays cool below 50c,
 In the PRINT_START I alter the target to 30c which it can never reach but causes a 100% fan while it tries thereby keeping the steppers cool.  On print end or print cancel,  the target temp is returned to 50c, slowing it down again.  It works very well, I can supply my printer.cfg if you want.

nicwilson58, 2024-11-09:
> Yes, I want your fan config :)

**Sorry for the delay was away for work,  Add it to you printer config like this:

Comment out original fan config  and add  new fan config which has target temp of 50c min speed of 50% these can be edited, its looking at the mcu temp,  fan will go 100% until mcu reaches 50c which will them drop it to 50%,  See furhter down for next parts.**

#[controller_fan board_fan]
#pin:U_1:PC4
#max_power:1.0
#shutdown_speed:1.0
#cycle_time:0.01
#fan_speed: 1.0
#heater:chamber
#stepper:stepper_x,stepper_y

[temperature_fan board_fan]
pin:U_1:PC4
max_power: 1.0
shutdown_speed: 1.0
cycle_time: 0.01
off_below: 0
sensor_type: temperature_host
control: pid
pid_deriv_time: 2.0
pid_Kp: 5
pid_Ki: 2
pid_Kd: 5
target_temp: 50
min_speed: 0.50
max_speed: 1.0
min_temp: 0
max_temp: 100

**To increase fan from 50% to 100% override the 50c target temp with a temp it can never reach but goes to 100% trying,  do this by adding this to PRINT_START**

SET_TEMPERATURE_FAN_TARGET TEMPERATURE_FAN=board_fan TARGET=30

On PRINT_END  &  CANCEL_PRINT  set back to 50c target temp by adding this:
SET_TEMPERATURE_FAN_TARGET TEMPERATURE_FAN=board_fan TARGET=50

**note I did not use idle timeout as for some reason it was never called.**
let me know how you go, it works great for me.

Closed 2024-12-04.

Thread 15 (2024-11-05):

Purpose and Effectiveness of Z_VIBRATE

jojolll, 2024-11-05:
Hi,

I’m wondering if anyone can explain the exact purpose of the Z_VIBRATE macro. Does it really improve print quality or stability? I’ve noticed that it could increases wear on the Z-axis.

Here is the code for the macro in question:

```
[gcode_macro Z_VIBRATE]
gcode:
    m204 S400
    G90
    G0 Z4
    G91
    #G4 P3000
    SET_PIN PIN=ctlyd VALUE=1
    {% for z in range(1,50) %}
        G1 Z1 F1200
        #G4 P50
        G1 Z-1 F1200
        #G4 P50
    {% endfor %}
    M204 S100
    SET_PIN PIN=ctlyd VALUE=0
    G4 P1000
    G1 Z4
    G90
```

The macro seems to vibrate the Z-axis by making small repeated movements, but I’m unsure if it provides any real benefit in terms of performance. Is it truly worth using considering that it can speed up wear on the Z-axis?

Sorry if this isn’t the right place to discuss this, but I’d appreciate any feedback or experiences on this!

Also, I’ve noticed that the homing process of the machine is NOT optimal. I’m currently working on optimizing this part. Would it be useful to submit a pull request if these settings improve the homing process compared to the original setup for the Qidi Plus 4?

jojolll, 2024-11-06:
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

Closed 2024-11-06.

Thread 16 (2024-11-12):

Recommended Gdstime fan is not really better

m4dm4n, 2024-11-12:
Comparing the specs between default heatsink fan and Gdstime, it's evident that the default one is better performer and quieter. So I don't really get why the other one i recommended.

Ruiapple RA-DC3010 24M
Current : 0.08A
Speed: 10000RPM
AirPressure: 4.2 CFM
Noise: 32dB

Gdstime GDA3010-5F 24V
Current : 0.06A
Speed: 12000RPM
AirFlow: 4.1 CFM
Noise: 35dB

spooknik, 2024-11-14:
Myself and @stew675 checked the model numbers of our stock fans which were RA-DC3010 M, which is only rated for 3.8CFM. I could be Qidi started shipping the more powerful version RA-DC3010 H which is on par with the GSDtime 3010. If you have a different model of fan stock on your printer, let us know.

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

https://www.fanscooling.com/dc-axial-fans/ra-dc3010.html

m4dm4n, 2024-11-14:
Granted, but I would always look at the official vendor specifications when comparing products:

https://www.ruiapple.cn/Products/DC-Axial-Fans/450.html

https://www.ruiapple.cn/uploads/soft/210810/3010.pdf

Yes, it's still the same model, but the specs on their page are a little different.

spooknik, 2024-11-15:
I don't have an accurate way to measure fan CFM, but the GSDtime fans push a lot more air than the stock fan even though the CFM ratings are close on paper. You can tell just by putting your hand on the other side of the hotend when the GSDtime fan is installed. It wouldn't be the first time specs on components are 'inflated'.

Either way, it seems the stock fan can keep up with cooling the cold side of the hotend with the newer ceramic heatbreak. So changing out the fan isn't as critical as it was for us on the initial units.

GSDtime isn't an A-tier supplier of fans, Sunon or Delta are better, but don't make 24V fans in 3010 size. So the GSDtime recommendation will stick around.

Closed 2024-11-15.

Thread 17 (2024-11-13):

Enabling KAMP Purging

rednet1, 2024-11-13:
I am using the new bleed line described, now I have a problem in a project I put as brim width 30 mm, the brim has passed above the bleed line

stew675, 2024-11-15:
Unfortunately the KAMP purging is performed by a Macro script on the printer itself, and is independent of the Gcode that your slicer emits.  There is no way to resolve this in the code.

One thing you can do is to watch the start of the print and flick the purge line out of the way immediately after it is laid down.

Closed 2024-11-15.

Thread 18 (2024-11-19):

Inconsistent CN links for replacement hotend heatsink fan

jaydenseric, 2024-11-19:
There are 2 CN links for a replacement hotend heatsink fan that I've discovered so far, and both are different:

1. https://github.com/qidi-community/Plus4-Wiki/blob/9aa1d78b20cca1841f9ef52bfa6b111f09b86f95/README.md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
2. https://github.com/qidi-community/Plus4-Wiki/blob/9aa1d78b20cca1841f9ef52bfa6b111f09b86f95/content/nozzle-clogging-tips/README.md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

The second one doesn't select a particular variation of 4 product options, which is correct?

What is the best link to purchase? Let's make them consistent in all locations.

stew675, 2025-01-29:
You are correct.  The AliExpress item does not match the other two, and in fact it appears to be changing over time.  I will remove that link.  I would suggest finding a GDSTime fan that matches the specs given on the EU shop page.  The US shop page is also correct, but it mistates the 12,000RPM as 1,200RPM, which is a typo.

stew675, 2025-01-29:
@spooknik I am unable to edit your file https://github.com/qidi-community/Plus4-Wiki/blob/9aa1d78b20cca1841f9ef52bfa6b111f09b86f95/content/nozzle-clogging-tips/README.md

Could you make the correction?

vega-d, 2025-02-18:
was fixed

Closed 2025-02-18.

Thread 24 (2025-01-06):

Problem chamber heater or normal?

patrick13010, 2025-01-06:
hello, i have adopted the following settings for my qidi plus 4 and noticed that the chamber heater only starts to work when the bed has reached almost 100° and the chamber has heated up to just under 45°. doesn't it make more sense for the bed and the chamber heater to be on together in order to heat up the chamber quickly?

content/tuning-for-40-percent-heater-power/README.md

stew675, 2025-01-29:
You are describing the stock behavior of the v1.6.0 firmware, where the chamber heater will only turn on once the print bed is 80C or higher.

Qidi have chosen to do this as it has been found that warm chamber temperatures will interfere with the accuracy of the piezo sensors under the bed that detect the Z-offset when the nozzle touches the bed during that probing phase.

Closed 2025-02-02.

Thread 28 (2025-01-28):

Updates for 1.6.0 firmware

MordantWastrel, 2025-01-28:
The 1.6.0 firmware makes some of the changes listed here standard (e.g. https://github.com/qidi-community/Plus4-Wiki/blob/main/content/chamber-heater-issue/README.md under 'setting the chamber_heater_power')

Do you want pull requests to:

* Trim these sections
* Add comments that they're no longer necessary if you're on the latest firmware
* ...?

Fantastic guide, thank you!

vega-d, 2025-02-18:
Yes. Feel free to open PRs with any contributions you want to make.

Closed 2025-02-18.

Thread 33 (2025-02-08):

Tweaking the meshbed accuracy changes for more speed while retaining tolerance and accuracy of probing

guykuo, 2025-02-08:
Thanks for the wonderful github on meshbed probing improvement. I have implemented those on my printer, but with some changes in values that might be helpful to other Plus 4 owners

As the github strives to achieve....

A. Increase Z stepper motor accuracy for both actual position and tracking of their position.

The Z and Z1 stepper motor microstepping is reduced to a more realistic 16. This increases their torque and improving how well their position tracking matches actual physical position. Interpolation is also turned off for those Z steppers to also make their motions more accurate.

B. Improve bed mesh probing accuracy and tolerance to variability in inductance probes.

C. Maximize speed of overall bed mesh process by accelerating motions that are not actual probe sampling motions.

**** CAVEAT: Back up your printer.cfg file before making these changes. Realize you could be making settings changes that could be really bad for your printer if you make a mistake.

Once you have completed the edits, you will need to "save and restart" for them to take effect.

All the setting changes are done in printer.cfg.

The following are my actual Plus 4 printer.cfg setting changes. Mine differ from the github suggestions.

I only list the settings that were changed. Leave the rest alone.

======= [stepper_z]

microsteps: 16

======= [stepper_z1]

microsteps: 16

======= [tmc2209 stepper_z]

interpolate: False

======= [tmc2209 stepper_z1]

interpolate: False

======= [smart_effector]

speed:3.25

lift_speed:18

samples: 1

sample_retract_dist: 6.5

samples_tolerance: 0.013

“Speed” is how fast the bed moves towards probe while the machine senses for bed. This speed originally 5 and github suggested 2.5 to improve accuracy. I tested a series of speeds and found 3.25 was a reasonable compromise that was slow enough to get repeatable readings, but not excessive prolong each probing motion.

“lift_speed” was increased from 5 to 18. “lift_speed” is how quickly the bed moves away from the probe. Measurements are not being done during the away motion and there is no reason this motion cannot be faster than the actual approach motion. I tried several increased lift_speed settings and kept it reasonable to not over stress the axis. A setting of 20 was particularly noisy. 18 was faster, but still quiet. Thus I settled on 18.

“samples” was changed to 1 AFTER doing tests with it at 2 samples / point to verify my speed and distance settings work for my probe.

“sample retract dist” is how far the bed moves away from probe when going after additional samples. Github suggests 10 mm, but because my probe was already OK with original 5 mm, I only increased it partially to improve tolerance to probe variability. If your probe is particulary odd, you may need to increase the distances out towards 10 mm. We want enough distance, but not so much that we excessively prolong probing motion.

“samples_tolerance” was tightened to 0.013 to help verify that distance and speed were working correctly. Tolerance is tested by machine ONLY if more than 1 sample / point specified. Once you have things verified, you can set samples down to 1 to nearly double speed, but verify settings with samples = 2 before dropping down to 1 sample.

=======

[bed_mesh]

speed: 400

horizontal_move_z: 6.5

“speed” is how fast x, y motions are performed during bed mesh. We have a fast core xy structure, so I boosted the motions to 400 from the stock 150.

“horizontal_move_z” is the baseline distance the bed is to be moved during probing. (If you change this value, you should also make “sample_retract_dist” in smart_effector match)

Github suggests 10 mm, but as noted in the smart_effector section, I compromised at 6.5 mm. My probe is probably a more typical one that is OK at 5 mm. Github suggests 10 mm to be tolerant of nearly all probes. I went with a shorter distance to get more speed while still tolerating more probe variability. If your particular probe needs more distance than 6.5 mm, you will notice probe values differ excessively during testing. In such case, increase the horizontal_move_z towards 10 mm.

=======

[z_tilt]

horizontal_move_z: 10

retries: 5

retry_tolerance: 0.013

Z-tilt distance I went with Github suggestion of 10 mm because there is little speed penalty for longer distances compared to that during bedmesh. Retries and retry_tolerance were matched to those in smart_effector.

Unkleskunky, 2025-02-09:
Awesome!

I am an early adopter but highly inexperienced 3d FDM'r. Even with my
Printrbot maker edition I had very few problems, my qidi plus 4 is worlds
more capable but still I have very few issues. I tend to print pretty
simple things with pretty practical materials but I would like to evolve.

I would like to learn to be comfortable making these kind of edits, can you
recommend a good starting point to learn this type of thing?

Much appreciated,

US

Much appreciated.

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

guykuo, 2025-02-13:
There is likely another place in the printer software that also needs the higher accuracy z-probing longer distance and slower speed.

There is also a gcode.macro.cfg file that has at least one command involved in probing for setting z. This seems to use speed and distance settings that are independent of those we adjust in printer.cfg.

Notice the line I show in orange. I think we should also change the speed and values in this to get more z probing accuracy during NON-bedmesh probes.

probe probe_speed=5 lift_speed=5 samples=5 sample_retract_dist=5

probably should be longer distance and slower speeds like....

probe probe_speed=**2.5** lift_speed=5 samples=5 sample_retract_dist=**10**

**

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

**

guykuo, 2025-02-17:
More data to consider. I'm now of the opinion that given a well behaving inductance probe, the probing distance is a more important factor tha probing speed in how accurately the probe repeats measurements.

Using a fixed probing speed of 2.5 mm/sec, I looked for inconsistencies in z-probing measurements during Z-homing while varying initial distahce to nozzle.

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

That series of measurements showed  z travel during probing of 5 mm is just within acceptable for my probe. The suggest value of 10 mm probing distance is more than required to get enough leeway. My use of 6.5 mm probing travel is above the distance needed and faster than traveling 10 mm for probing.

Next, I investigate speed of probing. The results were astonishing. The sweet spot in terms of fastest probing speed without increase standard deviation was about 12 mm/sec. That is far faster than the 2.5 mm/sec suggested or the 3.6 I have been using.

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

Given those results I validated the speed of 12 mm/sec on my machine and it words. Even detected a piece of debris beneath my print sheet. I set toleraance to  0.025 which is a bit tigher than 1/5 of my thinnest layer height. Validate with 2 samples/point and once that passed I set smart effectos as below...

[smart_effector]
pin:U_1:PC1
recovery_time:0
x_offset: 25
y_offset: 1.3
z_offset: 0.000001
speed: 12
lift_speed:18
probe_accel:50
samples: 1
samples_result: submaxmin
sample_retract_dist: 6.5
samples_tolerance: 0.025
samples_tolerance_retries:5

Also set bed_mesh to even faster non-probing motions

[bed_mesh]
speed: 600
horizontal_move_z: 6.5
mesh_min:25,10
mesh_max:295,295
probe_count:9,9
algorithm:bicubic
bicubic_tension:0.4
mesh_pps: 2,2

It works on my machine, but I spent hours validating my particular induction sensor.

Here is a full bed mesh being performed with these settings....
https://youtu.be/0GjVF6VDE3g

After that, had good success printing with a z-offset of zero (that is my usual z-offset for the particular machine specimen)

vega-d, 2025-02-18:
This looks very well researched and I agree, however the changes as you present them are not in a format that can be merged into the wiki. Please look at a guide for contributing to a github repo (for example, [this one](https://docs.github.com/en/get-started/exploring-projects-on-github/contributing-to-a-project?tool=webui)) and submit your changes as a pull request instead.

pravic, 2025-02-18:
> however the changes as you present them are not in a format that can be merged into the wiki.

And yet you closed this as "completed" which is quote misleading. Perhaps, it should be something else?

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

Closed 2025-02-18.

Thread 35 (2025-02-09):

KAMP Purging Instructions Should Delete Two More Lines from Machine Startup

guykuo, 2025-02-09:
Within machine start gcode, there are two gcode lines before the Qidi purge line code that should also be removed.

Those command the extruder move near bed at the left front of print object area and deposit a dot of filament.
That dot can be difficult to move - something anathema to the reason to replace the Qidi purge line with KAMP line.

With my print bed's excellent adhesion, the little dot is infuriatingly hard to remove, nearly as hard as the Qidi purge line.

The offending extruder move and extrude lines are show in red in attached image. They are...

G0 Z[initial_layer_print_height] F600
G1 E3 F1800

These two should be removed, in addiiton to replacing the orange lines with LINE_PURGE
Removal will get rid of that unwanted filament dot, but still allow LINE_PURGE to be work.
LINE_PURGE does its own extruder move prior to filament deposition.

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

shahvirb, 2025-02-10:
Submitted a PR here: https://github.com/qidi-community/Plus4-Wiki/pull/36

Closed 2025-02-10.

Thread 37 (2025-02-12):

Connecting the Carto PCB

jwestenberg, 2025-02-12:
Thank you for the great work making the carto available for the Qidi plus 4.

I have one question about the connection to the printer. Is it correct that the Carto PCB will be connected to the printer by USB and it is not possible to connect it to the PCB on the toolhead?

Does this mean the cable needs to be routed along the drag chain to either the usb port on the top or the one on the PCB where the Wifi dongle is usually attached?

Thank you for your help in advance.

vega-d, 2025-02-18:
qidi doesn't use can to communicate with the toolhead for carto to simply tap into existing wiring, so we must run a whole new usb cable whether we like it or not. Zip-tying the cable to the top of the dragchain *may* be the best option, but feel free to experiment.

Closed 2025-02-18.

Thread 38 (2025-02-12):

After SET_PRINT_STATS_INFO modification there are no layer infos (actual layer/total layers) and no slicer time on printer display and in Orca Slicer

GitHag42, 2025-02-12:
I updated to FW 1.6.0 and did some changes to the configuration as suggested here in the wiki.
With the new code for SET_PRINT_STATS_INFO from [here](https://github.com/qidi-community/Plus4-Wiki/tree/main/content/chamber-heater-issue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) I have no actual layer and no slicer time shown on the printer display and in Orca Slicer (Device tab) while printing. There are just dahes (--).

The code added at the top in gcode-macro.cfg is (as currently shown in the wiki article):

`
[gcode_macro SET_PRINT_STATS_INFO]
rename_existing: SET_PRINT_STATS_INFO_BASE
gcode:

    {% set curlayer =  params.CURRENT_LAYER|default(1)|int %}
    {% if (printer.toolhead.position.z) >= 268 %}
        # Set chamber target to 10C, which still keeps the chamber heater fan on
        # This allows the print bed to warm the chamber more effectively even
        # though the heater coils are effectively disabled
        M141 S10
    {% endif %}
    SET_PRINT_STATS_INFO_BASE CURRENT_LAYER={curlayer}
`
(I don't know how to put the hole macro in the code view here, so I added a new line after "gcode:" which is not present in my gcode-macro.cfg)

When I comment this code and restart the printer and start a new print the info is shown again.

Of course I followed the important [hint](https://github.com/qidi-community/Plus4-Wiki/tree/main/content/chamber-heater-issue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) for FW 1.6.0 and set target_min_temp: 10            #<--- Ensure that this field is set to 10C (default is 45C) in the [heater_generic chamber] config section.

Is the position where the code is added in gcode-macro.cfg important or am I missing something else here?

Thanks for any hints :-)

Ken6432, 2025-02-12:
For what it's worth, I have not made the referenced heater change to my 1.6 config, but seemingly randomly, I don't get the remaining time displayed during printing.  Sometimes it shows and sometimes it doesn't.  The issue may not be related to the changes made.

jwestenberg, 2025-02-18:
Could it be that it does not show layer information while using the "infill combination" setting?

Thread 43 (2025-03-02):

Can't blacklist Wifi Driver

JrothSKV, 2025-03-02:
Following the guide here on blacklisting the wifi driver and not having luck.  Trying to avoid opening up my printer for the 50th time.

https://github.com/qidi-community/Plus4-Wiki/blob/main/content/8188gu-blacklist/README.md

Can someone please validate whether this procedure is up to date?

(tried with wildcard first, then switched to explicit)

`mks@mkspi:~$ cat /etc/modprobe.d/blacklist-8188gu.conf`
`blacklist 8188gu`

`mks@mkspi:~$ lsmod | grep 8188gu`
`8188gu               1073152  0`
`cfg80211              876544  1 8188gu`

`mks@mkspi:~$ ps aux|grep -i rtw_cmd_thread && echo 'Module still loaded' || echo 'Module not loaded'
mks       2244  0.0  0.0   5948   644 pts/2    S+   21:47   0:00 grep -i rtw_cmd_thread
Module still loaded`

'mks@mkspi:~$ grep -r "8188gu" /etc/modules-load.d/ /lib/modules/$(uname -r)/
Binary file /lib/modules/5.16.20-rockchip64/modules.alias.bin matches
grep: /lib/modules/5.16.20-rockchip64/kernel/drivers/net/wireless/aic8800d80/aic8800d80_fdrv.ko: Permission denied
grep: /lib/modules/5.16.20-rockchip64/kernel/drivers/net/wireless/aic8800d80/aic_load_fw_d80.ko: Permission denied
Binary file /lib/modules/5.16.20-rockchip64/kernel/drivers/net/wireless/8188gu.ko matches
/lib/modules/5.16.20-rockchip64/modules.dep:kernel/drivers/net/wireless/8188gu.ko: kernel/net/wireless/cfg80211.ko.xz kernel/net/rfkill/rfkill.ko.xz
/lib/modules/5.16.20-rockchip64/modules.alias:alias usb:v0BDAp2005d*dc*dsc*dp*icFFiscFFipFFin* 8188gu
/lib/modules/5.16.20-rockchip64/modules.alias:alias usb:v0BDApB711d*dc*dsc*dp*icFFiscFFipFFin* 8188gu
Binary file /lib/modules/5.16.20-rockchip64/modules.dep.bin matches'

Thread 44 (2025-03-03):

Faster PRINT_START

jasc76, 2025-03-03:
Hi

could you offer a faster PRINT_START ? My plus4 takes like 7 minutes to start a print. It heats up and goes to nozzle cleaning. cools down the nozzle just to heat it up again. Then he homes and probes and homes again....

Cant this be streamlined !?

Regards
Jan

vega-d, 2025-04-06:
There's already a streamlined macro in the sister repo: https://github.com/qidi-community/config-xplus4/blob/main/start-print-overhaul.cfg

if you have ideas on how to improve it, pull requests are welcome!

Closed 2025-04-06.

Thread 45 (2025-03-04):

Bottom X axis rail is self-lubricating bronze, warn against oiling

mnemnion, 2025-03-04:
The [video here](https://old.reddit.com/r/QidiTech3D/comments/1j282k8/qidi_plus_4_extruder_lower_bushing_repair/) shows clearly that the lower X rail uses a graphite-plugged bronze bushing.  These are self-lubricating and should not have any oil added.

There's some language in the [lubing rods and screws](https://github.com/qidi-community/Plus4-Wiki/tree/main/content/lube-rods-screws) part of the wiki which warns against using grease or PTFE, which is true, but machine oil shouldn't go in there either.  Nothing but graphite should be on a graphite-lubed bushing, and it provides its own so regular maintenance shouldn't involve adding more (although that would itself be harmless to the bushing).

I think it would be better for that section to say something like this: "The bottom rod of the X axis uses a graphite plugged bronze bushing.  While the QidiTech maintenance video shows lube being applied to this rod, the graphite plugs provide the necessary lubrication and we believe adding oil is contraindicated.  If, over time, the bottom bushing squeaks, a small amount of graphite powder can be worked in, but this is likely to never happen".

I could be wrong here, maintaining shop tools is not my profession, but adding oil to a self-lubricating graphite bushing goes against everything I've learned and any reference on the Internet I can find.

Somewhat more speculatively (in that I couldn't find a primary source for this), adding some graphite powder should adsorb away any machine oil already added due to following the advice on the official wiki.  This would be a couple of rounds of light powdering, moving the tool head to work it in, wiping the gunk off the rail, waiting awhile for adsorption to occur, and repeating until the graphite is dry.   I don't endorse adding that to the wiki until it's been tried, I'm convinced it's perfectly safe, and reasonably confident it will work.  But I'm not going to contaminate my bottom rail with machine oil just to try cleaning it up, so this is an untested hypothesis.

dssamusaran, 2025-03-04:
Very interresting topic. It enticed me to do some googling around and it seems you're right.
Bottom rail should not be oiled or greased. Only cleaned with a rag.

The fact is my machine was already factory greased even on the bottom rail. So after very few prints I saw black gunk on the rail.
I went on Qidi wiki and followed their guide that indeed told me to grease the bottom rail. Which I'm doing like an idiot every now and then...

Would this kind of product work to try and clear up the grease following your method?
https://www.amazon.com.be/-/en/ProGraphite-Micronised-Graphite-lubricant-conductivity/dp/B07C75XTF2

I've absolutely never used graphite powder so I'd like to make sure it's the correct thing.
And I'll also wait for some more insight to see if the process seems good.

By the way, as of now I don't really have any black gunk buildup and the machine is working fine without squeaking.
Maybe I completely killed the graphite of my bushings?...

mnemnion, 2025-03-04:
> The fact is my machine was already factory greased even on the bottom rail.

It probably felt that way, yes. Might have been as well. I checked lubrication on all the moving parts before starting the machine, since if that step got skipped at the factory, it's bad news and I can easily prevent the problems by doing it myself.

It was only later in that thread, when `/u/pointclickfrown` pointed out the graphite plugs in the bushing, that I checked with a piece of paper towel, and that rod (only) is graphite lubricated.  The combination of graphite and machine oil does in fact look like black gunk, and it's not good.  It's not terrible either, but best to clean it out.

The product you linked to is the right kind of stuff, yes.  I wouldn't worry about the graphite wearing out, the bushings literally have [chunks of graphite added](https://www.bronzegleitlager.com/photo/ps35488774-self_lubricated_bronze_embedded_graphite_bushing_c86300_alloy.jpg) and should last at least as long as the toolhead.  You're probably fine if you just don't add more oil, but if you want to check, take white paper towel and gently rub the rod with it.  You should see smudged graphite, it looks exactly like smudge from a pencil because that's what pencil smudge is, the shade is quite distinctive.

That picture isn't the literal Plus 4 bushing btw, but it looks basically identical.

jojolll, 2025-03-14:
The sticker on the bottom of the machine specifically states that the bottom X axis should be lubricated with oil from time to time with graphite bushing, to avoid friction if it makes noise (which is never good).
I imagine that graphite alone is insufficient for the repeated and rapid friction of a 3D printer? Maybe that's the reason for the message?

I don't know what to make of that in terms of service life. I almost feel like continuing to add a drop of oil from time to time.

mrelwood, 2025-04-21:
> The sticker on the bottom of the machine specifically states that the bottom X axis should be lubricated with oil from time to time

Exactly. And there is a reason for the sticker being there.

We hunted for a solution with Qidi support for a month to bad print quality issues on a new Plus 4, which miraculously went away as soon as I cleaned up and oiled generously the lower X axis rod.

I get that a graphite bushing is used without lube in many instances, but a rapidly moving tool head doesn’t seem to be one of them.

stew675, 2025-07-15:
Closing this issue as it appears to have been resolved.  Good discussion above. @mrelwood's experiences echoes my own.  Oiling the lower graphite bearing with a *light* machine oil appears to solve issues with its grabbiness.

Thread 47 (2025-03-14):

Beacon Issues

MordantWastrel, 2025-03-14:
This issue is a catch-all for resources concerning the Beacon3D installation as described here: https://github.com/qidi-community/Plus4-Wiki/tree/main/content/bed-scanning-probes/Beacon3D/RevH-Normal

It is very much the case that plenty -- or even most -- users are having great success with their Beacon and there's no reason to think that there is a problem with these instructions so much as just the realization that not all printers are created equal and that, having now spent 4 full days installing, uninstalling, re-printing (I'm on my 4th mount), re-installing, re-testing, and at the end of all that I was better off before the beacon. There must be some reason for that and so this issue will hold information and links to pictures & videos to troubleshoot on the assumption that others might run into a similar issue.

Software config: Everything right out of https://github.com/qidi-community/Plus4-Wiki/tree/main/content/bed-scanning-probes/Beacon3D/RevH-Normal (including the entire printer.cfg that is supplied and nothing else).

The basic problem is that, post-Beacon, the slightest amount of stringing ends up being a huge problem. It is captured in this flow rate test I just did. The first layer looked right. Some were bad, most were good, as a flow rate test ordinarily would be. Then on the second layer, it went down to the bottom left box, which had a small amount of stringing. The beacon mount just grabbed the whole thing and moved it on top of one of the other boxes. I had to manually grab the filament ball under the nozzle and yank it out, and even then it only made it halfway through the print before repeating the issue on another box. Stringing that minor in a normal print would not 'spread' in that manner most of the time.

3 and a half minutes of the first layer being printed -- not much remarkable that I can see. The temp on my cool plate is normally 50 for PLA but despite defining it in Orca as being 50, it starts at 60 and then I have to drop it down; but this problem is unlikely to be caused by the plate being hotter than it needs to be (probably?)

Layer 1: https://photos.app.goo.gl/3pGtCSgyBpcvMGGY7

Layer 2 (after it's already knocked the bottom left one out of the way and is just carrying it along): https://photos.app.goo.gl/DEVx2PLq7Mv7Sekg7

Picture right after this:

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

Layer 3, where it starts to muck up another box: https://photos.app.goo.gl/4xHurn29vhfEKsJU6

Picture at the end after I aborted the print:

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

Now, not every print is like this; very simple ones where you can guarantee a great first layer are possibly / probably OK; I printed out a bed screw tool in PLA and it knocked the kamp purge line into the print but otherwise is OK. Still, it's not good if you can't run a flow rate calibration!

But @mordantWastrel, you say, just set a z-offset!

Well yeah, that's what I'm working on now, but where do you set it such that it will stay with the Beacon config? One person on Discord said you shouldn't have to set one (that being the whole point of the Beacon); others indicated that you need an initial z offset calibration with any setup (which makes sense). Do I add it to printer.cfg?

I should emphasize again that it's quite likely I've done something incorrectly; but if so, it's possibly others have as well as while I'm hardly a 3d printing guru, I'm at least marginally competent and had a great experience after getting everything dialed in pre-Beacon.

Thank you for help / input!

MordantWastrel, 2025-03-15:
I am closing this issue with a brief summary of what else was attempted:

* Z-offset values as described here: https://github.com/qidi-community/Plus4-Wiki/blob/main/content/bed-scanning-probes/Beacon3D/RevH-Normal/README.md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
* Setting `variable_probe_temp_delta` to 60C
* Trying different per-filament offsets (also recommended by Beacon3D support)

One or two other discord users on the Qidi Plus4 channel reported similar issues: sometimes you'd get a beautiful first layer over on this part of your bed but then it go haywire on another part, and once stringing occurs, it'd snowball from there. But not all of those users had exactly the setup from this wiki -- one was using a different mount and another had some customized macros. But I'll let them add to this issue (and re-open it if necessary).

Ultimately, the bed (pictured above) was deemed suspiciously smooth and my individual beacon the likely culprit, so it's going back to be exchanged.

Closed 2025-03-15.

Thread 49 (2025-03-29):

Z_TILT_ADJUST error

Jmjcoke, 2025-03-29:
I have an error after initial Z home and beacon check, x moves to left side of bed z move up toward nozzle and I get this error.

Internal error on command:"Z_TILT_ADJUST"
Once the underlying issue is corrected, use the
"FIRMWARE_RESTART" command to reset the firmware, reload the
config, and restart the host software.

I have compared print.cfg and gcode_macro.cfg to your examples.

any help would be appreciated.

Closed 2025-03-29.

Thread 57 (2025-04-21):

“Retry” and “Start over” options for SCREWS_TILT_CALCULATE

mrelwood, 2025-04-21:
The process starts with reverse homing to level the tilt of the bed. While this is an important step to do before tramming, it’s not precise enough to be done over and over again during subsequent retries. As a result, the adjustment values can vary as much as +/- 15 units even when only running the process again without making any adjustments.

The best solution I can think of are offering two options after having run the Calculate: “Retry” and “Start over”.

“Start over” would start the whole process from the beginning and include reverse homing, just like the current option does.

“Retry” would restart the process WITHOUT reverse homing.

I think it’s safe to assume that the bed frame tilt hasn’t changed enough during adjusting the screws to warrant new reverse homing that would just make the user run after a moving target when adjusting the screws.

Additionally I wish that the movement speeds would be more reasonable. The X and Y axis movements could be four times as fast as they currently are, and I think the Z axis could be doubled as well during reverse homing (for example fast movement to 260mm, then slow to the end.)

avdudchenko, 2025-04-22:
I genearly have found the screws tilt calculate to be a nightmare to use. It seems to be impossible to get the bed level with in 200 microns across four corners. If you do get it with 50 microns,, the next time you heat/cycle the bed it will be out of 200 microns again and the screw_tilt_calculate will complain.

I think the reason we want to leave the homing operation is it might be possible to twist the bed during the adjustment process. You do need to apply a bit of force/torque to break loose the lock nuts and twist adjustment screwes etc.

The fundamental issue to me seems the leveling blocks are not precise enough to retain level with in 10-50 microns) furthermore, expasnon of bed/screws/rubber supports varies enough to throw bed out of level by 100/200 microns.

So in general their issue is the tilt_screw_calculate threshold for whats level is overly optimistic and will make you waste a ton of time...

The 100-200 microns is not even that bad considering the size of the bed...

avdudchenko, 2025-04-22:
A follow on question, If we are always fighting left/right leveling, why do we not have a macro to simply "level" left right balance useign the two z - motors.

E.g. in theory we should only have to level bed front to back, and the left right should be correctable using the two z-motors. This would really simplify the whole process..... (I will need to look  into this).

TheRealBeef, 2025-05-22:
I think using the Z_tilt_adjust when doing the screws adjustment is a (potentially) bad idea, as this adjustment will happen on print_start and take out any slack

The idea of the screws adjustment is just to get the bed reasonably close so that bed meshing doesn't have to make overly large corrections

However, I can imagine a situation where a very crooked bed (such as the one that's out be >1mm I saw on the Discord yesterday) that will rack the bed sideways in order to be level and therefore won't show up in the screws tilt calculate macro.

The biggest sources of being off are
1. The bottom of the frame itself has 4 holes that the "legs" of the printer bed fit into, if there is junk in these it can push one of the legs upwards or downwards causing failed repeatability. This is why some recommend putting hardstops that raise this up slightly and give more repeatable results
2. There is some inherent error in homing against the bottom of the bed, as it may not be level enough even with such hardstops to be perfect. However, in my own experience I'm getting results that are generally not varying +/- 0.01mm with the occasional +/- 0.08mm run. One of the things that helps I think is tapping the bed after making the screw adjustments to try and eliminated any wiggle. Perhaps instead of adding the screws_tilt_calculated adding the vibrate macro that shakes the bed would do the same thing

avdudchenko, 2025-06-09:
Z_tilt_adjust  uses inductive probes to level left/right ,as such we do not need to worry about frame warp/or bottom stops etc.

I found that it helps a lot in speeding up how bet leaving, as you only need to do front to back level.

My issue still is that no matter how I tweak the induction probes I get poor reads. I need to make an issue on this as its unrelated.

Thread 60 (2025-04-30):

Can beacon safely disconnected during print without causing mcu shutdown error?

rhiz0matic, 2025-04-30:
The beacon rev-h is rated for 115c. I've had a couple of instances where I'm printing very slowly on a print bed that is 120c and the beacon overheats and disconnects, causing the printer to fault and request to reset the firmware once the mcu-beacon is reconnected (I just wait a minute or two to cool down and can resume the print if I shut off the switch and back on, so the printer thinks it's a power failure)

To avoid this. Is there a way to "disconnect" the beacon from the required mcu inputs during printing from the printer so that the printer will still run if it loses connection after the bed meshing is already complete and printing has begun?

stew675, 2025-05-01:
This would be a question better directed to the Beacon support staff.  As far as I am aware the Beacon unit is not able to be disconnected during a print, but they may have a solution.

The other suggestion would be to ensure that there is at least some small amount of air-flow over the beacon unit.  While the print bed may be 120C, the air in the chamber certainly is not, and it would not take very much airflow at all to ensure that the Beacon does not reach >115C

linouxis9, 2025-05-06:
@rhiz0matic Kalico (Danger Klipper) supports setting some MCU as optional (https://github.com/KalicoCrew/kalico/pull/339), with it, you could set the Beacon's MCU as optional / non-critical. If you know a bit of Python, you can try to backport this pull request to your Plus 4's klipper installation.

Closed 2025-05-20.

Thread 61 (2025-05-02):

Chamber Temperature Investigation and v1.6.0 Firmware

TheRealBeef, 2025-05-02:
https://github.com/qidi-community/Plus4-Wiki/blob/main/content/chamber-heater-investigation/README.md

Following the instructions here, I wanted to test the chamber heater to see if it functioned properly before doing a print, but seemingly no matter what I do the chamber heater refuses to turn on. I have the following in my printer.cfg - the v1.6.0 config is commented out in favor of the config presented. After this failed to work, I tried adding the following 3 lines from the original config, but this also didn't improve it.

`target_max_temp:65`
`heat_with_heater_bed:True`
`heat_with_heater_bed_tem_add:25`

Is there something that I'm missing?

```
# [heater_generic chamber]
# heater_pin:U_1:PC8
# max_power:0.4
# sensor_type:NTC 100K MGB18-104F39050L32
# sensor_pin:U_1:PA1

# control = pid
# pid_Kp=63.418
# pid_Ki=1.342
# pid_Kd=749.125

# min_temp:-100
# max_temp:70
# target_min_temp:45
# target_max_temp:65
# heat_with_heater_bed:True
# heat_with_heater_bed_tem_add:25

[temperature_sensor chamber_probe]
sensor_type:NTC 100K MGB18-104F39050L32
sensor_pin:U_1:PA1

[heater_generic chamber]
heater_pin:U_1:PC8
max_power:0.4
control = pid
pid_Kp=63.418
pid_Ki=1.342
pid_Kd=749.125
min_temp:-100
max_temp:80
target_min_temp:10
target_max_temp:65
sensor_type: temperature_combined
sensor_list: temperature_sensor GD32, temperature_sensor chamber_probe, temperature_sensor GD32, temperature_sensor GD32
combination_method: mean
maximum_deviation: 70
heat_with_heater_bed:True
heat_with_heater_bed_tem_add:25
```

rhiz0matic, 2025-05-21:
just curious what your solution was?

TheRealBeef, 2025-05-22:
At the time (with new printer) I wasn't aware that Qidi disables the heater unless the bed it at its setpoint and >70c.

So I just wasn't familiar with how the system was intended to function.

Closed 2025-05-21.

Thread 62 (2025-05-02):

Receiving "COMBINED SENSOR temperature 70.0 above maximum temperature of 70.0." The Firmware is Shutdown.

ch3atarah, 2025-05-02:
I've attached a snip of the error. This happens when I'm trying to print ASA (prints for just a little, then hits this error). Any help is appreciated. Basic config:
Implemented most of all the tweaks.
Bed = 105
Nozzle = 255
Chamber= 65

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

rhiz0matic, 2025-05-02:
try changing your max chamber temperature setting in the printer.cfg file to 75

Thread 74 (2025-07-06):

Chamber Heater fan issue proposal

Palasito, 2025-07-06:
Recently had to print PA12-CF and tried to use the chamber heater.
Heater came on, fan started spinning (albeit slowly, but did not think about it twice) and after waiting for a while I got the error that the heater is not heating at an expected rate. Checked for new firmware (no update performed was already on latest) ,restarted the printer and the second time the fan would not turn on, chamber heater sensor went to 130 degrees celcius after a while triggering a thermal shutdown.
After some fiddling around I found out that by pushing the fan in place using a toothpick it would actually start spinning (and reaching higher speeds that what I thought 100% was previously).

This led to searching google extensively and finding out [this](https://www.printables.com/model/1081513-qidi-plus-4-chamber-heater-fan-kickstand/) model.

While the model was printing I actually had the same thought as the guy in the first comment [here](https://www.printables.com/model/1081513-qidi-plus-4-chamber-heater-fan-kickstand/comments) Rimvydas Kiaulakis.

Actually took apart my fan, raised the magnet as he proposes, tested the outcome (turning the fan on by manipulating it to activate when using the bed heater and not the chamber heater), after the magnet was in the correct place (way higher that i thought it would need) glued it in place with an epoxy glue that had lying around and it is working great ever since having printed almost 3kg of PA12-CF now.

Would be great if there was a writeup about that in the Plus4-Wiki as it seems it's something at least 3 ppl experienced and many more might be exepriencing but are attributing the issue to the generic chamber heater issues

P.S. got some pictures for the writeup if they are needed

Palasito, 2025-09-14:
I am not proposing to trigger the chamber heater fan from the bed heater! Just outlined my troubleshooting steps in order to help someone if experiencing issues to check whether they have the same problem!

The writeup I am suggesting is the "fix" with the epoxy glue in the fan in order for people with tech skills to not actually go and buy new fans thinking that their old fans are broken!

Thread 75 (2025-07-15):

Had to delete some lines from gcode_macro.cfg otherwise Klipper wouldn't boot ...

IrishJay, 2025-07-15:
As in the title, following the instructions for the Plus 4, Klipper threw a "can't run ..." error for the macros. I tracked down the offending lines to:

    { action_respond_info("Applying Z offset adjustment for hotend temperature of %.1f°C" % hotend_temp|float) }
    { action_respond_info("  Offset Correction    = %.3f" % (offset_correction)|float) }
    { action_respond_info("  Reference Position   = %.1f" % (reference_position)|float) }
    { action_respond_info("  Target Position      = %.6f" % (target_position)|float) }

For some reason, these wouldn't successfully comment out in the file but when removed, the system booted and beacon runs fine.

IrishJay, 2025-07-16:
If I add the full section for [gcode_macro _APPLY_NOZZLE_OFFSET] it throws the following exception:

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

Code pasted here: https://pastebin.com/XCuyveqz

Thanks for the rapid reply - other than this (and its probably a macro I won't use) everythign worked brilliantly

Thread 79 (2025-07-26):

BEST instructions on how to add a second camera to a QIDI+4

coziman-vt, 2025-07-26:
I searched for at least 2 days to get this information.

If we are using original QIDI+4 software packages we are using an old version of Buster - so no CrowsNest - and there is very little specifically relevant Klipper or Moonsail information for our situation with webcamd.

The following link leads to an article that WORKS.
https://www.reddit.com/r/QidiTech3D/comments/1hz6yga/qidi_q1_pro_adding_a_second_camera/

With several items of note:

1. We already have cameras so you have to delete the 'Settings' file for the existing one.
Then when you restart after editing both webcam.txt and webcam2.txt you will re-add BOTH cameras.

2. Don't edit Line 69  - you edit Line 72 for the url. This must be from a change in the base webcam.txt config file.

3. When you copy the camera Device ID's from Putty, SSH or  Fluidd device listing, you should paste them into a text app and MAKE SURE there are no extra spaces at the beginning or in the middle of the address (and only one space between -d and the /dev)

YMMV.
Chris

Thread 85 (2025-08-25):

Debian 10 at End Of Life

jetmech43, 2025-08-25:
I tried to update my Linux distro on the Qidi Plus 4 and got hit with several errors that Debian "buster' is at EOL and will  no longer receive updates. To update you would have to upgrade to Debian 11 first "bullseye" , then to Debian 12 "bookworm". I am not sure how this will effect future python dependencies or security to the printer but IMO it is something that needs to be addressed before there is a major problem. Thank You.

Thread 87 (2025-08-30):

Beacon H install - home_xy_position cannot be used with [homing_override]

JohnnyPicnic, 2025-08-30:
After editing my files I get the following. Also tried the config examples.

`Config error
Traceback (most recent call last):
  File "/home/mks/klipper/klippy/klippy.py", line 175, in _connect
    self._read_config()
  File "/home/mks/klipper/klippy/klippy.py", line 141, in _read_config
    self.load_object(config, section_config.get_name(), None)
  File "/home/mks/klipper/klippy/klippy.py", line 130, in load_object
    self.objects[section] = init_func(config.getsection(section))
  File "/home/mks/klipper/klippy/extras/beacon.py", line 3841, in load_config
    return get_beacons(config).get_or_add_sensor(None)
  File "/home/mks/klipper/klippy/extras/beacon.py", line 3764, in get_or_add_sensor
    return self.add_sensor(name)
  File "/home/mks/klipper/klippy/extras/beacon.py", line 3750, in add_sensor
    self.sensors[name] = sensor = BeaconProbe(cfg, BeaconId(name, self))
  File "/home/mks/klipper/klippy/extras/beacon.py", line 117, in __init__
    self.homing_helper = BeaconHomingHelper.create(self, config)
  File "/home/mks/klipper/klippy/extras/beacon.py", line 2395, in create
    return BeaconHomingHelper(beacon, config, home_xy_position)
  File "/home/mks/klipper/klippy/extras/beacon.py", line 2404, in __init__
    "home_xy_position cannot be used with [%s]" % (section,)
configparser.Error: home_xy_position cannot be used with [homing_override]`

Closed 2025-08-30.

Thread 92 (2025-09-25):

Set Piezo Sensors to Reasonble Pre-tension

halentech, 2025-09-25:
There are a lot of mistakes from my point of view:
_bed screw knobs to position the bottom of the plastic knobs to 9-10 mm away from bottom of metal bed plate above_
Distance is still same, if you leave 3 therads or 8 threads at the bottom of knob as example. Only change is in threads count, not distance to the metal plate! It's still same. In mine it's about 10.8mm. You should measure, (I'am not sure what), bot no distance to the plate. It's defined by knob height at all.

Next is when leaving front left knob alone. In my printer, even I do platform reset and set middle point to pass 0.15mm and take measure metal plate, then front left knob is too close to the bed. You must in first set front left knob and left all others alone.  Only pres next, next next and do it again in same. Finally, then repeat procedure, but leave front left alone and set up three others.
After this procedure, it's repeated calibration steps and +- same result.

 original setup steps:
4. Set Piezo Sensors to Reasonble Pre-tensionBefore doing any bed leveling, set bed screw knobs to position the bottom of the plastic knobs to 9-10 mm away from bottom of metal bed plate above. If your printer has just the locking nut (no lock washer), that leaves about three threads visible below lock nut. Once at this position, lock the front left screw in place. Leave that screw alone. Do bed leveling ONLY with the other three screws. That should keep you in good pre-tension range for all four piezos.

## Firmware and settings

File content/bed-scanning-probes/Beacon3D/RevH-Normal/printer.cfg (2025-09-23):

# QIDI Plus4 V1.0.0

[include plr.cfg]
[include gcode_macro.cfg]
[include time_update.cfg]

# Plugins
[include timelapse.cfg]
[include KAMP_Settings.cfg]

[printer]
kinematics:corexy
max_velocity: 600
max_accel: 20000
max_accel_to_decel: 10000
max_z_velocity: 20
max_z_accel: 500
square_corner_velocity: 5

[mcu]
serial: /dev/ttyS2
restart_method: command
baud:500000

[mcu U_1]
serial: /dev/ttyS0
restart_method: command
baud:500000

[temperature_sensor GD32]
sensor_type: temperature_mcu
sensor_mcu: mcu

[temperature_sensor mainboard_stm32]
sensor_type: temperature_mcu
sensor_mcu: U_1

[temperature_sensor mainboard_rockchip]
sensor_type: temperature_host

[respond]
default_type: echo

[gcode_arcs]
resolution: 0.5

[exclude_object]

[save_variables] 
filename =/home/mks/printer_data/config/saved_variables.cfg

[adxl345]
cs_pin:PA4
spi_software_sclk_pin:PA5
spi_software_mosi_pin:PA7
spi_software_miso_pin:PA6
axes_map: -x, z, -y

[resonance_tester]
accel_per_hz: 150
max_smoothing:0.1

[output_pin sound]
pin:PA1
value:0

[duplicate_pin_override]
pins:

[bed_screws]
screw1: 25,21
screw1_name: Front left
screw2: 285,21
screw2_name: Front right
screw3: 285,281
screw3_name: Last right
screw4: 25,281

[screws_tilt_adjust]
screw1: 25,21
screw1_name: Front left
screw2: 25,21
screw2_name: Front right
screw3: 285,281
screw3_name: Back right
screw4: 25,281
screw4_name: Back left
screw_thread: CW-M4

[gcode_macro SCREWS_TILT_CALCULATE]
rename_existing: _SCREWS_TILT_CALCULATE_BASE
gcode:
    { action_respond_info("starting screw rotation calculation...") }
    M141 S0 # disable chamber heater (see https://github.com/qidi-community/Plus4-Wiki/tree/main/content/chamber-heater-issue)
    M4031
    G28
    Z_TILT_ADJUST
    _SCREWS_TILT_CALCULATE_BASE

[hall_filament_width_sensor]
adc1: PA2
adc2: PA3
cal_dia1: 1.50
cal_dia2: 2.0
raw_dia1: 14197
raw_dia2: 15058
default_nominal_filament_diameter: 1.75
max_difference: 0
measurement_delay: 50
enable: false
measurement_interval: 10
logging: False
min_diameter: 0.3
use_current_dia_while_delay: False
pause_on_runout:True
runout_gcode:
            RESET_FILAMENT_WIDTH_SENSOR
            M118 Filament run out
event_delay: 3.0
pause_delay: 0.5

[extruder]
step_pin:PB9
dir_pin:PB8
enable_pin:!PC15
rotation_distance: 53.7  #22.6789511 Bondtech 5mm Drive Gears
gear_ratio: 1517:170
microsteps: 64
full_steps_per_rotation: 200 #200 for 1.8 degree, 400 for 0.9 degree
nozzle_diameter: 0.400
filament_diameter: 1.75
min_temp: 0
max_temp: 380
min_extrude_temp: 175
smooth_time: 0.2
heater_pin:PB3
sensor_type:MAX6675
sensor_pin:PB12
spi_speed: 100000
spi_software_sclk_pin:PB13
spi_software_mosi_pin:PA11
spi_software_miso_pin:PB14
max_power: 1
control : pid  
pid_Kp=33.555
pid_Ki=4.76
pid_Kd=59.141
pressure_advance: 0.032
pressure_advance_smooth_time: 0.05
max_extrude_cross_section: 500
instantaneous_corner_velocity: 5.000
max_extrude_only_distance: 1000.0
max_extrude_only_velocity: 5000
max_extrude_only_accel: 5000
step_pulse_duration: 0.000002

[tmc2209 extruder]
uart_pin:PC13
interpolate: False
#run_current: 0.75
run_current: 0.714
stealthchop_threshold: 0

[stepper_x]
step_pin:U_1:PB4
dir_pin:!U_1:PB3
enable_pin:!U_1:PB5
microsteps: 16
rotation_distance: 38.86
full_steps_per_rotation:200 # set to 400 for 0.9 degree stepper
endstop_pin:tmc2240_stepper_x:virtual_endstop
position_min: -1.2
position_endstop: -1.2
position_max:307
homing_speed:50
homing_retract_dist:0
homing_positive_dir:False
step_pulse_duration:0.0000001

[tmc2240 stepper_x]
cs_pin:U_1:PD2
spi_software_sclk_pin:U_1:PA5
spi_software_mosi_pin:U_1:PA7
spi_software_miso_pin:U_1:PA6
spi_speed:200000
run_current: 1.07
# hold_current: 0.5
interpolate: True
stealthchop_threshold:0
diag0_pin:!U_1:PB8
driver_SGT:1

[stepper_y]
step_pin:U_1:PC14
dir_pin:!U_1:PC13
enable_pin:!U_1:PC15
microsteps: 16
rotation_distance: 38.86
full_steps_per_rotation:200 # set to 400 for 0.9 degree stepper
endstop_pin:tmc2240_stepper_y:virtual_endstop
position_min: -2
position_endstop: -2
position_max:325
homing_speed:50
homing_retract_dist:0
homing_positive_dir:False
step_pulse_duration:0.0000001

[tmc2240 stepper_y]
cs_pin:U_1:PB9
spi_software_sclk_pin:U_1:PA5
spi_software_mosi_pin:U_1:PA7
spi_software_miso_pin:U_1:PA6
spi_speed:200000
run_current: 1.07
#hold_current: 0.5
interpolate: True
stealthchop_threshold:0
diag0_pin:!U_1:PC0
driver_SGT:1

[stepper_z]
step_pin:U_1:PB1
dir_pin:U_1:PB6
enable_pin:!U_1:PB0
microsteps: 16
rotation_distance: 4
full_steps_per_rotation: 200
endstop_pin: probe:z_virtual_endstop # U_1:PC3 for Z-max, or Beacon
endstop_pin_reverse:tmc2209_stepper_z:virtual_endstop
#position_endstop:1
position_endstop_reverse:285
position_max:285
position_min: -4
homing_speed: 10
homing_speed_reverse: 10
second_homing_speed: 5
#homing_retract_dist: 5.0
homing_retract_dist: 0
homing_positive_dir:false
homing_positive_dir_reverse:true
#step_pulse_duration:0.0000001

[tmc2209 stepper_z]
uart_pin:U_1: PB7
run_current: 1.07
# hold_current: 0.17
interpolate: False
stealthchop_threshold: 99999
diag_pin:^U_1:PA13
driver_SGTHRS:100

[stepper_z1]
step_pin:U_1:PC10
dir_pin:U_1:PA15
enable_pin:!U_1:PC11
microsteps: 16
rotation_distance: 4
full_steps_per_rotation: 200
endstop_pin_reverse:tmc2209_stepper_z1:virtual_endstop
#step_pulse_duration:0.0000001

[tmc2209 stepper_z1]
uart_pin:U_1: PC5
run_current: 1.07
# hold_current: 0.17
interpolate: False
stealthchop_threshold: 99999
diag_pin:^U_1:PC12
driver_SGTHRS:100

[heater_bed]
heater_pin: U_1:PB10
sensor_type:NTC 100K MGB18-104F39050L32
sensor_pin:U_1: PA0
max_power: 1.0
control = pid
pid_Kp= 63
pid_Ki= 1.5
pid_Kd= 750
pwm_cycle_time:0.001
min_temp: -60
max_temp: 125

[temperature_sensor chamber_probe]
sensor_type:NTC 100K MGB18-104F39050L32
sensor_pin:U_1:PA1

[heater_generic chamber]
heater_pin:U_1: PC8
max_power: 0.5
pwm_cycle_time: 0.135335
control= pid
pid_Kp= 63
pid_Ki= 1.5
pid_Kd= 750
min_temp: -100
max_temp: 75
sensor_type: temperature_combined
sensor_list: temperature_sensor GD32, temperature_sensor chamber_probe, temperature_sensor GD32, temperature_sensor GD32
combination_method: mean
maximum_deviation: 70

[verify_heater chamber]
max_error: 300
check_gain_time:1200
hysteresis: 5
heating_gain: 1

[temperature_sensor Chamber_Thermal_Protection_Sensor]
sensor_type:NTC 100K MGB18-104F39050L32
sensor_pin:U_1:PC2
min_temp:-100
max_temp:130

[verify_heater extruder]
max_error: 120
check_gain_time:20
hysteresis: 5
heating_gain: 1

[verify_heater heater_bed]
max_error: 200
check_gain_time:360
hysteresis: 10
heating_gain: 1

[fan_generic auxiliary_cooling_fan]
pin: U_1:PA8
shutdown_speed: 1.0
cycle_time: 0.0100
hardware_pwm: false
kick_start_time: 0.100
off_below: 0.0

[fan_generic chamber_circulation_fan]
pin: U_1:PC9
shutdown_speed: 1.0
cycle_time: 0.0100
hardware_pwm: false
kick_start_time: 0.100
off_below: 0.0

[chamber_fan chamber_fan]
pin:U_1:PA4
max_power: 1.0
shutdown_speed: 1.0
kick_start_time: 0.5
heater:chamber
fan_speed: 1.0
off_below: 0
idle_timeout:60
idle_speed:1.0

[heater_fan hotend_fan]
pin:PB5
max_power: 1.0
shutdown_speed:1.0
kick_start_time: 0.5
heater: extruder
heater_temp: 50.0
fan_speed: 1.0
off_below: 0

[heater_fan hotend_fan2]
pin:PB4
max_power: 1.0
shutdown_speed:1.0
kick_start_time: 0.5
heater: extruder
heater_temp: 50.0
fan_speed: 1.0
off_below: 0

[heater_fan hotend_fan3]
pin:PB10
max_power: 1.0
shutdown_speed:1.0
kick_start_time: 0.5
heater: extruder
heater_temp: 50.0
fan_speed: 1.0
off_below: 0

[fan_generic cooling_fan]
pin:PA8
max_power: 1.0
shutdown_speed:0
cycle_time: 0.010
hardware_pwm: False
kick_start_time: 0.100
off_below: 0.0
tachometer_pin:PA9
tachometer_ppr: 2
tachometer_poll_interval: 0.0015

[temperature_fan cpu_fan]
pin:U_1:PC4
max_power: 1.0
shutdown_speed: 1.0
cycle_time: 0.01
off_below: 0
sensor_type: temperature_host
control: pid
pid_deriv_time: 5.0
pid_Kp: 5
pid_Ki: 2
pid_Kd: 5
target_temp: 45
min_speed: 0.4
max_speed: 1.0
min_temp: 0
max_temp: 90

#[controller_fan board_fan]
#pin:U_1:PC4
#max_power:1.0
#shutdown_speed:1.0
#cycle_time:0.01
#fan_speed: 1.0
#stepper:stepper_x,stepper_y

[output_pin caselight]
pin: U_1:PC7
pwm: false
shutdown_value:1
value:1

[output_pin beeper]
pin:U_1: PA2
pwm: false
shutdown_value:0
value:0

[output_pin ctlyd]
pin:U_1: PA14
pwm: false
shutdown_value:0
value:0

[z_tilt]
z_positions:
    -17.5,152.5
    335.7,152.5

points:
    50, 171.3           # Assumes using stew675 beacon mount's offsets
    255, 171.3          # Assumes using stew675 beacon mount's offsets

speed: 200
horizontal_move_z: 5
retries: 5
retry_tolerance: 0.006

[bed_mesh]
speed: 150
horizontal_move_z: 2
zero_reference_position: 152.5, 152.5
mesh_min: 22,22
mesh_max: 283,283
probe_count: 14,14
algorithm:bicubic
bicubic_tension: 0.3
mesh_pps: 2,2
fade_start: 2
fade_end: 10
fade_target: 0
split_delta_z: 0.01
move_check_distance: 4
#adaptive_margin: 5
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

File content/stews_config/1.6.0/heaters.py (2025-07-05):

# Tracking of PWM controlled heaters and their temperature control
#
# Copyright (C) 2016-2020  Kevin O'Connor <kevin@koconnor.net>
#
# This file may be distributed under the terms of the GNU GPLv3 license.
import os, logging, threading


######################################################################
# Heater
######################################################################

KELVIN_TO_CELSIUS = -273.15
MAX_HEAT_TIME = 5.0
AMBIENT_TEMP = 25.
PID_PARAM_BASE = 255.

class Heater:
    def __init__(self, config, sensor):
        self.printer = config.get_printer()
        self.name = config.get_name().split()[-1]
        # Setup sensor
        self.sensor = sensor
        self.target_min_temp = config.getfloat('target_min_temp', 0.)
        self.target_max_temp = config.getfloat('target_max_temp', 999.)
        self.heat_with_heater_bed = config.getboolean("heat_with_heater_bed", False)
        self.heat_with_heater_bed_tem_add = config.getfloat('heat_with_heater_bed_tem_add', 0.)
        self.min_temp = config.getfloat('min_temp', minval=KELVIN_TO_CELSIUS)
        self.max_temp = config.getfloat('max_temp', above=self.min_temp)
        self.sensor.setup_minmax(self.min_temp, self.max_temp)
        self.sensor.setup_callback(self.temperature_callback)
        self.pwm_delay = self.sensor.get_report_time_delta()
        # Setup temperature checks
        self.min_extrude_temp = config.getfloat(
            'min_extrude_temp', 170.,
            minval=self.min_temp, maxval=self.max_temp)
        is_fileoutput = (self.printer.get_start_args().get('debugoutput')
                         is not None)
        self.can_extrude = self.min_extrude_temp <= 0. or is_fileoutput
        self.max_power = config.getfloat('max_power', 1., above=0., maxval=1.)
        self.smooth_time = config.getfloat('smooth_time', 1., above=0.)
        self.inv_smooth_time = 1. / self.smooth_time
        self.lock = threading.Lock()
        self.last_temp = self.smoothed_temp = self.target_temp = 0.
        self.last_temp_time = 0.
        # pwm caching
        self.next_pwm_time = 0.
        self.last_pwm_value = 0.
        # Setup control algorithm sub-class
        algos = {'watermark': ControlBangBang, 'pid': ControlPID}
        algo = config.getchoice('control', algos)
        self.control = algo(self, config)
        # Setup output heater pin
        heater_pin = config.get('heater_pin')
        ppins = self.printer.lookup_object('pins')
        self.mcu_pwm = ppins.setup_pin('pwm', heater_pin)
        pwm_cycle_time = config.getfloat('pwm_cycle_time', 0.100, above=0.,
                                         maxval=self.pwm_delay)
        self.mcu_pwm.setup_cycle_time(pwm_cycle_time)
        self.mcu_pwm.setup_max_duration(MAX_HEAT_TIME)
        # Load additional modules
        self.printer.load_object(config, "verify_heater %s" % (self.name,))
        self.printer.load_object(config, "pid_calibrate")
        gcode = self.printer.lookup_object("gcode")
        gcode.register_mux_command("SET_HEATER_TEMPERATURE", "HEATER",
                                   self.name, self.cmd_SET_HEATER_TEMPERATURE,
                                   desc=self.cmd_SET_HEATER_TEMPERATURE_help)
    def set_pwm(self, read_time, value):
        if self.target_temp <= 0.:
            value = 0.
        if ((read_time < self.next_pwm_time or not self.last_pwm_value)
            and abs(value - self.last_pwm_value) < 0.05):
            # No significant change in value - can suppress update
            return
        pwm_time = read_time + self.pwm_delay
        self.next_pwm_time = pwm_time + 0.75 * MAX_HEAT_TIME
        self.last_pwm_value = value
        self.mcu_pwm.set_pwm(pwm_time, value)
        #logging.debug("%s: pwm=%.3f@%.3f (from %.3f@%.3f [%.3f])",
        #              self.name, value, pwm_time,
        #              self.last_temp, self.last_temp_time, self.target_temp)
    def temperature_callback(self, read_time, temp):
        with self.lock:
            time_diff = read_time - self.last_temp_time
            self.last_temp = temp
            self.last_temp_time = read_time
            temp_diff = temp - self.smoothed_temp
            adj_time = min(time_diff * self.inv_smooth_time, 1.)
            self.smoothed_temp += temp_diff * adj_time
            self.can_extrude = (self.smoothed_temp >= self.min_extrude_temp)
            # Use the smoothed temperature if smooth time is >1.0s, otherwise use
            # the instantaneous temperature instead - stew675 - 2025/07/03
            update_temp = (temp, self.smoothed_temp)[bool(self.smooth_time > 1.0)]
            self.control.temperature_update(read_time, update_temp, self.target_temp)

        toolhead = self.printer.lookup_object("toolhead")
        curtime = self.printer.get_reactor().monotonic()
        position_z = toolhead.get_position()[2]
        if position_z > 270. and "xyz" in toolhead.get_status(curtime)["homed_axes"]:
            heaters = self.printer.lookup_object("heaters")
            heater = heaters.lookup_heater("chamber")
            if heater.target_temp > 0.:
                heaters.set_temperature(heater, 0.)
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

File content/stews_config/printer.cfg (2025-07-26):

# Stew's unedited printer.cfg for Qidi Plus 4

[include plr.cfg]
[include gcode_macro.cfg]
[include time_update.cfg]

# Plugins
[include timelapse.cfg]
[include KAMP_Settings.cfg]
[include box.cfg]

[printer]
kinematics:corexy
max_velocity: 600
max_accel: 20000
max_accel_to_decel: 10000
max_z_velocity: 20
max_z_accel: 500
square_corner_velocity: 5

[mcu]
serial: /dev/ttyS2
restart_method: command
baud:500000

[mcu U_1]
serial: /dev/ttyS0
restart_method: command
baud:500000

[temperature_sensor GD32]
sensor_type: temperature_mcu
sensor_mcu: mcu

[temperature_sensor mainboard_stm32]
sensor_type: temperature_mcu
sensor_mcu: U_1

#[temperature_sensor mainboard_rockchip]
#sensor_type: temperature_host

[respond]
default_type: echo

[gcode_arcs]
resolution: 0.5

[exclude_object]

[save_variables] 
filename =/home/mks/printer_data/config/saved_variables.cfg

[pause_resume]

[display_status]

[gcode_macro_break]

[virtual_sdcard]
path: ~/printer_data/gcodes
on_error_gcode:CANCEL_PRINT
    
[print_stats]

[force_move]
enable_force_move : True

[output_pin sound]
pin:PA1
value:0

[output_pin caselight]
pin: U_1:PC7
pwm: false
shutdown_value:1
value:1

[output_pin beeper]
pin:U_1: PA2
pwm: false
shutdown_value:0
value:0

[output_pin ctlyd]
pin:U_1: PA14
pwm: false
shutdown_value:0
value:0

[hall_filament_width_sensor]
adc1: PA2
adc2: PA3
cal_dia1: 1.50
cal_dia2: 2.0
raw_dia1: 14197
raw_dia2: 15058
default_nominal_filament_diameter: 1.75
max_difference: 0
measurement_delay: 50
enable: false
measurement_interval: 10
logging: False
min_diameter: 0.3
use_current_dia_while_delay: False
pause_on_runout:True
runout_gcode:
            RESET_FILAMENT_WIDTH_SENSOR
            M118 Filament run out
            {% set can_auto_reload = printer.save_variables.variables.auto_reload_detect|default(0) %}
            {% if can_auto_reload == 1 %}
              AUTO_RELOAD_FILAMENT
            {% endif %}
event_delay: 3.0
pause_delay: 0.5

[extruder]
step_pin:PB9
dir_pin:PB8
enable_pin:!PC15
rotation_distance: 53.7         # Qidi Extruders
#gear_ratio: 1628:170           # X3-series straight cut stepper motor
gear_ratio: 1517:170            # Plus4 helical cut stepper motor
microsteps: 128
full_steps_per_rotation: 200    #200 for 1.8 degree, 400 for 0.9 degree
nozzle_diameter: 0.400
filament_diameter: 1.75
min_temp: 0
max_temp: 380
min_extrude_temp: 175
smooth_time: 0.2
heater_pin:PB3
sensor_type:MAX6675
sensor_pin:PB12
spi_speed: 100000
spi_software_sclk_pin:PB13
spi_software_mosi_pin:PA11
spi_software_miso_pin:PB14
max_power: 1
control : pid
pid_Kp=44
pid_Ki=12
pid_Kd=12
pressure_advance: 0.032
pressure_advance_smooth_time: 0.05
max_extrude_cross_section: 500
instantaneous_corner_velocity: 5.000
max_extrude_only_distance: 1000.0
max_extrude_only_velocity: 5000
max_extrude_only_accel: 5000
step_pulse_duration: 0.000002

[tmc2209 extruder]
uart_pin:PC13
interpolate: True
run_current: 0.75
#run_current: 0.714
stealthchop_threshold: 0

[verify_heater extruder]
max_error: 120
check_gain_time:20
hysteresis: 5
heating_gain: 1

[stepper_x]
step_pin:U_1:PB4
dir_pin:!U_1:PB3
enable_pin:!U_1:PB5
microsteps: 64
rotation_distance: 38.90
full_steps_per_rotation:200 # set to 400 for 0.9 degree stepper
endstop_pin:tmc2240_stepper_x:virtual_endstop
position_min: -1.2
position_endstop: -1.2
position_max:307
homing_speed:50
homing_retract_dist:0
homing_positive_dir:False
step_pulse_duration:0.0000001

[tmc2240 stepper_x]
cs_pin:U_1:PD2
spi_software_sclk_pin:U_1:PA5
spi_software_mosi_pin:U_1:PA7
spi_software_miso_pin:U_1:PA6
spi_speed:400000
run_current: 1.15
# hold_current: 0.5
interpolate: False
stealthchop_threshold:0
diag0_pin:!U_1:PB8
driver_SGT:1

[stepper_y]
step_pin:U_1:PC14
dir_pin:!U_1:PC13
enable_pin:!U_1:PC15
microsteps: 64
rotation_distance: 38.90
full_steps_per_rotation:200 # set to 400 for 0.9 degree stepper
endstop_pin:tmc2240_stepper_y:virtual_endstop
position_min: -2
position_endstop: -2
position_max:325
homing_speed:50
homing_retract_dist:0
homing_positive_dir:False
step_pulse_duration:0.0000001

[tmc2240 stepper_y]
cs_pin:U_1:PB9
spi_software_sclk_pin:U_1:PA5
spi_software_mosi_pin:U_1:PA7
spi_software_miso_pin:U_1:PA6
spi_speed:400000
run_current: 1.15
#hold_current: 0.5
interpolate: False
stealthchop_threshold:0
diag0_pin:!U_1:PC0
driver_SGT:1

[stepper_z]
step_pin:U_1:PB1
dir_pin:U_1:PB6
enable_pin:!U_1:PB0
microsteps: 16
rotation_distance: 4
full_steps_per_rotation: 200
endstop_pin: probe:z_virtual_endstop        # U_1:PC3 for Z-max, or Beacon
endstop_pin_reverse:tmc2209_stepper_z:virtual_endstop
#position_endstop:1
position_endstop_reverse:285
position_max:285
position_min: -4
homing_speed: 10
homing_speed_reverse: 10
second_homing_speed: 5
homing_retract_dist: 0
homing_positive_dir:false
homing_positive_dir_reverse:true

[tmc2209 stepper_z]
uart_pin:U_1: PB7
run_current: 1.07
interpolate: False
stealthchop_threshold: 99999
diag_pin:^U_1:PA13
driver_SGTHRS:100

[stepper_z1]
step_pin:U_1:PC10
dir_pin:U_1:PA15
enable_pin:!U_1:PC11
microsteps: 16
rotation_distance: 4
full_steps_per_rotation: 200
endstop_pin_reverse:tmc2209_stepper_z1:virtual_endstop

[tmc2209 stepper_z1]
uart_pin:U_1: PC5
run_current: 1.07
interpolate: False
stealthchop_threshold: 99999
diag_pin:^U_1:PC12
driver_SGTHRS:100

[heater_bed]                                    # The print bed heater unit
heater_pin: U_1:PB10
sensor_type:NTC 100K MGB18-104F39050L32
sensor_pin:U_1: PA0
max_power: 1.0
control: pid
smooth_time: 5
pid_Kp: 100
pid_Ki: 0.6
pid_Kd: 0
pwm_cycle_time: 0.001
min_temp: -60
max_temp: 125

[verify_heater heater_bed]
max_error: 200
check_gain_time:360
hysteresis: 10
heating_gain: 1

#[temperature_sensor chamber_probe]
#sensor_type:NTC 100K MGB18-104F39050L32
#sensor_pin:U_1:PA1

[temperature_sensor Chamber_Thermal_Protection_Sensor]    # The thermal probe within the chamber heater unit
sensor_type:NTC 100K MGB18-104F39050L32
sensor_pin:U_1:PC2
min_temp:-100
max_temp:130

[duplicate_pin_override]
pins: U_1:PA1

[heater_generic chamber]                        # Controls the PTC heater coils within the chamber heater unit
heater_pin:U_1: PC8
max_power: 0.6
pwm_cycle_time: 0.135335
control: pid
smooth_time: 30
pid_Kp: 60
pid_Ki: 0.12
pid_Kd: 0
min_temp: -100
max_temp: 85
sensor_type:NTC 100K MGB18-104F39050L32
sensor_pin:U_1:PA1

[verify_heater chamber]
max_error: 300
check_gain_time:1200
hysteresis: 5
heating_gain: 1

[chamber_fan chamber_fan]                       # Controls the blower fan within the chamber heater unit
pin:U_1:PA4
max_power: 1.0
shutdown_speed: 1.0
kick_start_time: 0.5
heater:chamber
fan_speed: 1.0
off_below: 0
idle_timeout:300
idle_speed:1.0

[temperature_fan chamber_circulation_fan]       # Controls the axial fan that exhausts air from the printer
pin:U_1:PC9
max_power: 1.0
shutdown_speed: 1.0
cycle_time: 0.01
hardware_pwm: False
kick_start_time: 0.5
off_below: 0.25
control: pid
pid_deriv_time: 10.0
pid_Kp: 100
pid_Ki: 0
pid_Kd: 0
target_temp: 50
min_speed: 0.2
max_speed: 1.0
min_temp: -100
max_temp: 85
sensor_type:NTC 100K MGB18-104F39050L32
sensor_pin:U_1:PA1

[fan_generic auxiliary_cooling_fan]             # Controls the large blower fan on the right side of print chamber
pin: U_1:PA8
shutdown_speed: 1.0
cycle_time: 0.0100
hardware_pwm: false
kick_start_time: 0.100
off_below: 0.0

[temperature_fan mainboard_rockchip]            # Controls the fan on the mainboard cover that cools the mainboard
pin:U_1:PC4
max_power: 1.0
shutdown_speed: 1.0
cycle_time: 0.01
off_below: 0
sensor_type: temperature_host
control: pid
pid_deriv_time: 4.0
pid_Kp: 50
pid_Ki: 0
pid_Kd: 0
target_temp: 50
min_speed: 0.4
max_speed: 1.0
min_temp: 0
max_temp: 90

[heater_fan hotend_fan]                         # Controls the fan that cools the hotend heatsink
pin:PB5
max_power: 1.0
shutdown_speed:1.0
kick_start_time: 0.5
heater: extruder
heater_temp: 50.0
fan_speed: 1.0
off_below: 0

[heater_fan hotend_fan2]                        # Optional 2-pin fan port (unpopulated)
pin:PB4
max_power: 1.0
shutdown_speed:1.0
kick_start_time: 0.5
heater: extruder
heater_temp: 50.0
fan_speed: 1.0
off_below: 0

[heater_fan hotend_fan3]                        # Optional 2-pin fan port (unpopulated)
pin:PB10
max_power: 1.0
shutdown_speed:1.0
kick_start_time: 0.5
heater: extruder
heater_temp: 50.0
fan_speed: 1.0
off_below: 0

[fan_generic cooling_fan]                       # This is the Part Cooling Fan
pin:PA8
max_power: 1.0
shutdown_speed: 1.0
cycle_time: 0.020
hardware_pwm: False
kick_start_time: 0.100
off_below: 0.0
tachometer_pin:PA9
tachometer_ppr: 2
tachometer_poll_interval: 0.001

[bed_screws]
screw1: 25,21
screw1_name: Front left
screw2: 285,21
screw2_name: Front right
screw3: 285,281
screw3_name: Last right
screw4: 25,281

[screws_tilt_adjust]
screw1: 25,21
screw1_name: Front left
screw2: 25,21
screw2_name: Front right
screw3: 285,281
screw3_name: Back right
screw4: 25,281
screw4_name: Back left
screw_thread: CW-M4

[z_tilt]
z_positions:
    -17.5,152.5
    335.7,152.5
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

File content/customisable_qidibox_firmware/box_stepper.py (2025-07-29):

from kinematics import extruder
import chelper
from . import force_move
import math
from . import box_extras as be
from . import led

HOMING_START_DELAY = 0.001
ENDSTOP_SAMPLE_TIME = .000015
ENDSTOP_SAMPLE_COUNT = 4
DISABLE_DELAY = 0.05

class BoxExtruderStepper:
    def __init__(self, config):
        #ExtruderStepper
        self.printer = config.get_printer()
        self.extruder_stepper = extruder.ExtruderStepper(config)
        self.stepper = self.extruder_stepper.stepper

        self.stepper_name = config.get_name().split()[1]
        #RunOutButton
        runout_pin = config.get('runout_pin')
        runout_button = be.BoxButton(config, runout_pin, self.runout_button_callback)
        self.r_endstop_state = 0
        self.slot_not_unload = True
        # #RunOutEndstop
        self.r_endstop = be.BoxEndstop(config, self.stepper_name + "_runout", runout_pin, True)
        self.r_endstop.add_stepper(self.stepper)

        #ManualStepper
        self.reactor = self.printer.get_reactor()
        self.next_cmd_time = 0.
        ffi_main, ffi_lib = chelper.get_ffi()
        self.trapq = ffi_main.gc(ffi_lib.trapq_alloc(), ffi_lib.trapq_free)
        self.trapq_append = ffi_lib.trapq_append
        self.trapq_finalize_moves = ffi_lib.trapq_finalize_moves
        self.box_extras = self.printer.load_object(config, 'box_extras')
        self.b_endstop = self.box_extras.b_endstop
        self.e_endstop = self.box_extras.e_endstop
        self.b_endstop.add_stepper(self.stepper)
        self.e_endstop.add_stepper(self.stepper)
        self.b_motion = self.box_extras.b_motion
        stepper_enable = self.printer.lookup_object('stepper_enable')
        self.se = stepper_enable.lookup_enable(self.stepper.get_name())

        #Command
        self.print_stats = self.printer.lookup_object('print_stats')
        self.stepper_num = int(self.stepper_name.replace('slot', ''))
        label_map = {
            0: '1A', 1: '1B', 2: '1C', 3: '1D',
            4: '2A', 5: '2B', 6: '2C', 7: '2D',
            8: '3A', 9: '3B', 10: '3C', 11: '3D',
            12: '4A', 13: '4B', 14: '4C', 15: '4D'
        }
        self.stepper_label = label_map[self.stepper_num]

        self.gcode = self.printer.lookup_object('gcode')
        self.gcode.register_mux_command('SLOT_UNLOAD', "SLOT", self.stepper_name, self.cmd_SLOT_UNLOAD)
        self.gcode.register_mux_command('EXTRUDER_LOAD', "SLOT", self.stepper_name, self.cmd_EXTRUDER_LOAD)
        self.gcode.register_mux_command('EXTRUDER_UNLOAD', "SLOT", self.stepper_name, self.cmd_EXTRUDER_UNLOAD)
        self.gcode.register_mux_command('SLOT_PROMPT_MOVE', "SLOT", self.stepper_name, self.cmd_SLOT_PROMPT_MOVE)
        self.gcode.register_mux_command('RFID_READ', "SLOT", self.stepper_name, self.cmd_SLOT_RFID_READ)

        #Led
        self.led = led.PrinterPWMLED(config)
        self.red_value = 0
        self.white_value = 0
        self.led_timer = self.reactor.register_timer(self.set_led)
        self.printer.register_event_handler("klippy:ready", self.led_handle_connect)

        #RFID_STATE
        self.rfid_state=0

        #BOX_DRYING_STATE
        self.is_drying = False

    #RunOutButton
    def runout_button_callback(self, eventtime, state):
        if self.is_drying:
            return
        self.r_endstop_state = state
        if self.print_stats.state == "printing" and state:
            runout_num = self.box_extras.get_value_by_key('runout_' + str(self.stepper_num), 0)
            self.box_extras.save_variable('runout_' + str(self.stepper_num), runout_num + 1)
        if state:
            self.box_extras.save_variable(self.stepper_name, 0)
            if self.print_stats.state == "printing" and self.stepper_name == self.box_extras.get_value_by_key("slot_sync", "slot-1"):
                self.gcode.run_script("SET_FILAMENT_SENSOR SENSOR=box_motion_sensor ENABLE=0")#
        else:
            self.box_extras.save_variable(self.stepper_name, 3)
            if self.box_extras.can_load_slot and self.slot_not_unload:
                self.gcode.run_script("RELOAD_ALL RFID=1 FIRST=" + str(self.stepper_num) + "\nM400\n")
    def get_status(self, eventtime=None):
        return {'runout_button': self.r_endstop_state,
                "rfid_state": self.rfid_state,}
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

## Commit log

2024-10-14 improve chamber heating issue macro
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2024-10-14 Update README.md
    Added some of my printable mods
    Added links for 3010 fan and 80mm fan
    Added Lubing idler bearing video
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2024-10-15 Change trigger height to 268mm
    Based upon some testing, and adding in something of a "safety margin", I've increased the trigger height for turning off the heater at 268mm. This is at about the point where the thermal protection s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
    Rather than turning it off too early, or waiting until the absolute last moment to turn the heater off, which may risk triggering a thermal shutdown, we'll turn it off at the latest point before the 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
    This means that the printer will only have to "coast" for the last 12mm of Z travel.
2024-10-15 Correct text to match 268mm
    Missed updating the text to match the new 268mm trigger point.
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2024-10-15 Replace 0.2mm JSON file with Raw Link
    Allows right click in the link and save under.
2024-10-19 Confirmed 262mm is highest Z without issues
2024-10-19 Added chamber thermal sensor mount model
    Marked as a WIP for now
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2024-10-25 Added line to reset main chamber target
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2024-10-29 Update README.md
    Updated target temp from 45c to 50c to allow for an upgraded 40mm fan to manage board temps in typical ambient conditions.
    Added info and link to a tested 4020 fan that will allow for reuse of the stock mainboard cover while still significantly increasing airflow.
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2024-11-01 Update README.md
    Fix button link
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2024-11-13 Drop Z stepper micro-steps to 16
    This change aligns with the better bed meshing discussion
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2024-12-29 Update config for Firmware 1.6.0
    As per https://github.com/qidi-community/Plus4-Wiki/blob/main/content/chamber-heater-issue/README.md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
    We likely need this new line due to firmware 1.6.0 changes.
2025-01-04 Improve set_affinity handling
    Improve thread handling for set_affinity()
    This now appropriately handles all threads for all running processes, and not just the first process
    It also appropriately handles the situation where the named process does not exist
2025-01-21 Add Cartographer3D
    [carto.cfg]
2025-01-30 Add files via upload
    Changes performed to printer.cfg to get BeaconH working
    [printer.cfg]
2025-01-30 Added mount STEP and STL files
    [Combo-Mount.step]
2025-01-31 Update Carto
    [carto.cfg]
2025-01-31 Tweaked clearances on mount model
    [Combo-Mount.step]
2025-02-04 Update printer.cfg
    Uncomment force_move for PLR, and some UI move ops to work right
    [printer.cfg]
2025-02-04 Update gcode_macro.cfg
    Give descriptions to most macros.
    Modified various UI macros to work right with Beacon
    [gcode_macro.cfg]
2025-02-04 Update README.md
    Updated to keep force_move uncommented, and modified various macros to support all current Printer Screen UI operations in a manner compatible with Beacon
2025-02-06 Relocate Stews BeaconH install guide
    [Combo-Mount.step, gcode_macro.cfg, printer.cfg]
2025-02-06 Fix path to probe.py
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2025-02-07 Update to Carto
    [carto.cfg]
2025-02-09 Added fix for Filament Loading
    The hotend was heating up for homing causing the beacon portion of homing to fail due to being overtemp.
2025-02-09 Fix nozzle too hot warnings
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2025-02-14 using 3 in 1 oil with ptfe is not good for the graphite bearing
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2025-02-24 Extra exclusion zone protection
    [Line_Purge.cfg]
2025-02-24 Conditional exclusion zone protection
    [Line_Purge.cfg]
2025-02-24 Update gcode_macro.cfg with _Z_VIBRATE
    [gcode_macro.cfg]
2025-02-28 Conditional Wiping and Purging for CLEAR_NOZZLE
    A set of macros for the CLEAR_NOZZLE operations that breaks the various steps into their component sub-operations.
    This allows for various operations to be conditionally called, to avoid performing things like purging, wiping onto the PEI plate and so on.
2025-03-05 Add missing HOTEND parameters
    [gcode_macro.cfg]
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2025-03-14 Comment out shaketune in example printer.cfg
    If we're including a sample printer.cfg for beacon, it should probably contain only things we can reasonably assume everybody has (e.g. items from the wiki) -- if shaketune is in there and the user doesn't have shaketune installed it will error on startup.
    [printer.cfg]
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2025-04-07 Corrected SCREWS_TILT_CALCULATE label
2025-04-07 Add cameras to qidi plus4 (#52)
    * Create adding_additional_cameras
    * Create adding_cameras
    * Delete content/adding_additional_cameras
    * Update adding_cameras
    * Add files via upload
    * Delete content/add-additional-cameras/fluidd with multiple cameras.jpg
    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
2025-04-13 Camera, PEI Collision, and Z-Offset Improvement (#55)
    * Delete content/Kuo Steps for Reliable Z-Offset directory
    * Delete content/prevent-nozzle-collision-with-PEI-cooling-platform directory
    * Delete content/add-additional-cameras directory
    * Delete content/prevent-nozzle-collision-with-PEI-cooling-platform directory
    * Delete content/Kuo Steps for Reliable Z-Offset directory
    * Delete content/prevent-nozzle-collision-with-PEI-cooling-platform directory
    * Delete content/add-additional-cameras directory
    * Create README.md
    * Update README.md
    * Create README.md
    * Update README.md
    * Create README.md
    * Update README.md
    * Add files via upl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
2025-05-07 Format changes and step enrichments (#58)
    Inserted a comment about `[screws_tilt_adjust]` sections
    * Clarify screws-tilt-calculate
    Added as per suggestion of avdudchenko
    * Update markdown and text for System Tuning
    * Update Enable KAMP Purging
    - I added some screenshots, altered some remarks to use NOTE/TIP/WARNING/CAUTION make up
    - Added a "Reboot Printer" section.
    - Added SSH alternative
    * Update KAMP Purge README.md
    Typo
    * Create disable QIDIL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
2025-05-09 Remove Beacon_Calibrate include
    It's no longer used anyway
    [printer.cfg]
2025-05-10 Update README.md
    Corrected description of what happens with the hotend after calling `SCREW_ADJUST_START`
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2025-05-21 Update KAMP_Settings.cfg
    Adjust maximums
    [KAMP_Settings.cfg]
2025-05-21 Update Line_Purge.cfg
    Tweak Purge locations
    [Line_Purge.cfg]
2025-05-21 Update gcode_macro.cfg
    Various Tweaks
    [gcode_macro.cfg]
2025-05-21 Update printer.cfg
    Stepper tweaks
    [printer.cfg]
2025-06-12 Update gcode_macro.cfg
    Improved exhaust temperature fan handling
    [gcode_macro.cfg]
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2025-06-24 Change probe_temp_delta to 75
    [gcode_macro.cfg]
2025-06-24 Conditional Homing and Better Chamber Temp Control
    [gcode_macro.cfg]
2025-06-24 Some cleanup
    [printer.cfg]
2025-06-24 wip: fix temperature results
2025-06-28 Clean up CANCEL_PRINT behaviour
    [gcode_macro.cfg]
2025-06-29 Improved high chamber temperature handling
    [gcode_macro.cfg]
2025-06-29 Adjust limits to handle printing PPS-CF
    [printer.cfg]
2025-06-29 Fix typos
    [gcode_macro.cfg]
2025-06-29 Better PRINTER_INIT settings on exhaust fan
    [gcode_macro.cfg]
2025-07-04 Custom heater.py
    Replaces /home/mks/klipper/klippy/extras/heaters.py
    Uses the smooth temperature for PID algorithm when smooth_time > 1s
    [heaters.py]
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2025-07-05 Tightened integration of exhaust fan with chamber heater
    [gcode_macro.cfg]
2025-07-05 Improve PID handling of chamber and bed
    [printer.cfg]
2025-07-05 Accidentally uploaded older config
    [printer.cfg]
2025-07-05 Re-ording of PRINT_START sequence
    [gcode_macro.cfg]
2025-07-07 More exhaust/chamber heater integration fiddling
    [gcode_macro.cfg]
2025-07-07 Just refreshing config upload
    [printer.cfg]
2025-07-07 Fix bad config reference
    [gcode_macro.cfg]
2025-07-19 QidiBox Support
    [gcode_macro.cfg]
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2025-07-22 Remove beacon_calibrate.cfg include
    [printer.cfg]
2025-07-24 Update Cartographer guide for 1.7
    [carto.cfg, gcode_macro.cfg, printer.cfg]
2025-07-26 Small corrections
    [carto.cfg, gcode_macro.cfg, printer.cfg]
2025-07-27 Fixed pause-unpause and power loss recovery by changes to the homing_override macro. Small fixes where found when proofreading.
    [gcode_macro.cfg]
2025-07-27 Removed doubled Z_TILT_ADJUST from PRINT_START
    [gcode_macro.cfg]
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2025-08-03 Changed links to .py files, included missing klipper requierments.
2025-08-13 Update gcode_macro.cfg
    Limit acceleration during bed meshing in G29
    [gcode_macro.cfg]
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2025-08-13 Update gcode_macro.cfg
    Fix typo. Add comments
    [gcode_macro.cfg]
2025-09-23 Set home_y_before_x to true
    Set home_y_before_x to true
    [printer.cfg]
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2025-10-21 Update for 1.7.2 & remove calibration on each G29
    [gcode_macro.cfg]
2025-10-26 Adding buttons_irq.py, which got turned from a .py file in 1.7.1 to .so in 1.7.2. Also adding SSH commands for file replacement.
2025-11-02 Add macros directly to box_macros.cfg
    [box_macros.cfg]
2026-01-02 Update Beacon manual, add screws_tilt_adjust section
    My Beacon mount was out of bounds, resulting in `!! No trigger on probe after full movement` error.
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
